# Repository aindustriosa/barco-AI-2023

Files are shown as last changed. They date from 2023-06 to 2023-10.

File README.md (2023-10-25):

# Barco Solar AI-023 A Industriosa
Barco Solar AI-023 A Industriosa

Hemos creado un barco impreso en 3d para participar en la <a href="http://regatasolar.org" target="_blank">Regata Solar de Marine Instruments</a>. Esta vez un trimaran de unos 4Kg de peso y un volumen total de 12 litros.

Se ha diseñado integramente en Cinema 4D, con subdivisión de superficies (curvas Nurbs).

Una vez modelado, se han dividio en 32 piezas para imprimir, secciones de hasta 250x250x200mm y exportado a STL. Para optimizar la impresión intentamos que cada sección no tardase más de 10 horas en imprimirse, para intentar imprimir por el dia y dormir por la noche :P El software de slicer usado es el Simplify3D y la impresora una Ender 5 Plus.

Evitanto el uso de soportes a la hora de imprimir se han hecho algunas secciones que finalmente se pegan para poder imprimir sobre el lado más plano y evitar luego el postprocesado.

Una vez impresas las piezas, y para facilitar la rigidez a la hora de pegarlas, se han hecho unas secciones en cada pieza para pegar y encajar unos pequeños tubos impresos de unos 10x10x50mm. Se ha pegado todas las partes con pegamento para modelismo comprado en bazar chino, tarda unas 4 horas en secar y quedan las piezas muy rígidas. En las zonas que por sharping de las piezas hizo falta se relleno de masilla para carrocerías de Ceys. 

Para darle el acabado final, una vez pegadas todas las piezas, se ha aplicado imprimación de color blanco y posteriormente una mano de Epoxi. En el montaje, en las zonas más irregulares se le aplicó un poco de lijado.

Para encajar las partes de electrónica al barco, así como el soporte de la placa solar, se han usado unos insertos de M5 y M3 aplicados con solador, que evitan el uso de tuercas y hacen que las zonas de enrosque queden bien sujetas.

Para las tapas se ha usado goma Eva cortado en laser para hacer las zonas de unión impermeables.

## Electrónica

Hemos intentado hacer una nueva PCB partiendo de un Attiny1614. Se ha diseñado la pcb en KiCAD, integrando un sensor INA219 para la optimización del voltaje y potencia de la placa solar basandonos en la propuesta de <a href="https://github.com/aindustriosa/Solar_MPPT_board" target="_blank">A Industriosa</a> del año 2019.

Con los limites de potencia y memoria del Attiny1614, hemos implementado el uso del sensor así como un divisor de voltaje para leerlo via VREF. Los mensajes enviados desd eel mando RC al receptor, son procesados por el microcontrolador y en caso de exigirle una velocidad mayor al 30% entra en modo automático, y prioriza el rendimiento que este generando la placa solar en ese momento a optener la velocidad optima sin permitir la caida de potencia por un exceso del rendimiento de la placa solar.

## Materiales

8x PETG 1Kg Blanco 1.75mm (<a href="https://www.amazon.es/dp/B08C4YP5RS/ref=twister_B08HSFRV2M?_encoding=UTF8&th=1" target="_blank">Amazon</a>)

1x Smartfil FLEX - Filamento Flexible (<a href="https://www.smartmaterials3d.com/flex-filamento#/1-tamano-s_330g/26-diametro-175_mm/29-color-sapphire" target="_blank">Smart Materials 3D</a>)
  
3x Tubos cuadrados de 10x10x500mm - <a href="https://www.clipcarbono.com/es/home/947-tubo-exterior-cuadrado-10x10-mm-interior-cuadrado-8x8-mm-de-fibra-de-carbono-longitud-1000-mm.html" target="_blank">Tubo cuadrado, exterior (10x10 mm.) - interior (8x8 mm.) de fibra de carbono - Longitud 1000 mm.</a> Cortesía de <a href="https://www.clipcarbono.com" target="_blank">ClipCarbono</a>

1x Castropox 4307/1209 Resina Epoxi de usos generales (<a href="https://www.castrocompositesshop.com/es/resinas/1099-resina-epoxi-castropox-43071209.html" target="_blank">Castro Composites</a>)

1x Masilla Carrocerias Ceys (<a href="https://www.amazon.es/Desconocido-M59016-Adhesivo-masilla-carrocerias/dp/B00ITVXML6" target="_blank">Amazon</a>)

3x Imprimación Plástico (<a href="https://www.amazon.es/MTN-IMPRIMACIÓN-PLÁSTICOS-400-ML/dp/B00WG2K6W2/ref=sr_1_15?__mk_es_ES=ÅMÅŽÕÑ&crid=2E2QZXNCDXAI6&keywords=imprimacion&qid=1655512005&sprefix=imprimacion%2Caps%2C124&sr=8-15" target="_blank">Amazon</a>)

1x soporte helice y timón (<a href="https://es.aliexpress.com/item/32901476708.html" target="_blank">Aliexpress</a>)

100x Inserto roscado M3 (<a href="https://www.amazon.es/gp/product/B08BCRZZS3/ref=ppx_yo_dt_b_asin_title_o00_s00?ie=UTF8&th=1" target="_blank">Amazon</a>)

6x Inserto roscado M5 (<a href="https://www.amazon.es/gp/product/B07YSVXWS8/ref=ppx_yo_dt_b_asin_title_o00_s00?ie=UTF8&th=1" target="_blank">Amazon</a>)

1x Acoplamiento Motor 4x5mm (<a href="https://www.amazon.es/gp/product/B09LV3KD4H/ref=ppx_yo_dt_b_asin_title_o05_s00?ie=UTF8&th=1" target="_blank">Amazon</a>)

1x Motor NTM Prop Drive 28-30 800KV (<a href="https://hobbyking.com/es_es/propdrive-v2-2830-800kv-brushless-outrunner-motor.html" target="_blank">Hobbyking</a>)

1x Turnigy Multistart 20A V2 ESC (<a href="https://hobbyking.com/es_es/turnigy-multistar-20a-v2-esc-with-blheli-and-4a-lbec-2-6s.html" target="_blank">Hobbyking</a>)

## Enlaces

- <a href="http://regatasolar.org" target="_blank">Regata Solar de Marine Instruments</a>
- <a href="https://www.clipcarbono.com" target="_blank">ClipCarbono</a>
- <a href="http://aindustriosa.org" target="_blank">A Industriosa</a>

Proxecto patrocinado por Xunta de Galicia e Amtega Axencia para a Modernización Tecnolóxica

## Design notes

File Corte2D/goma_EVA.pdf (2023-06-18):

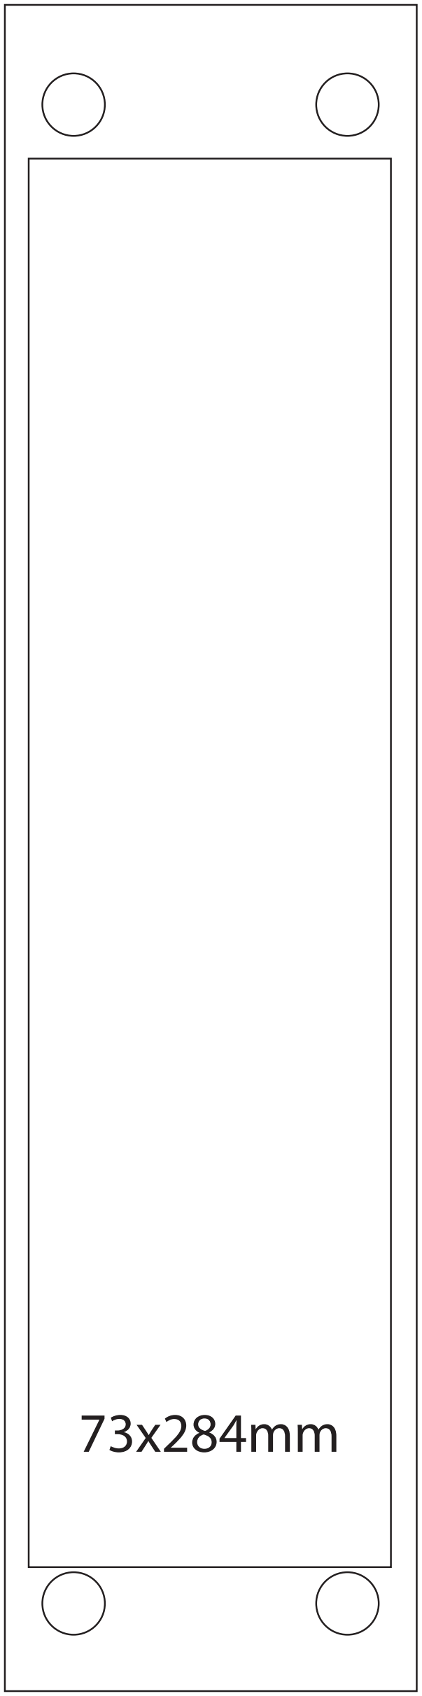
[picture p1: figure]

83x340mm

8x72mm

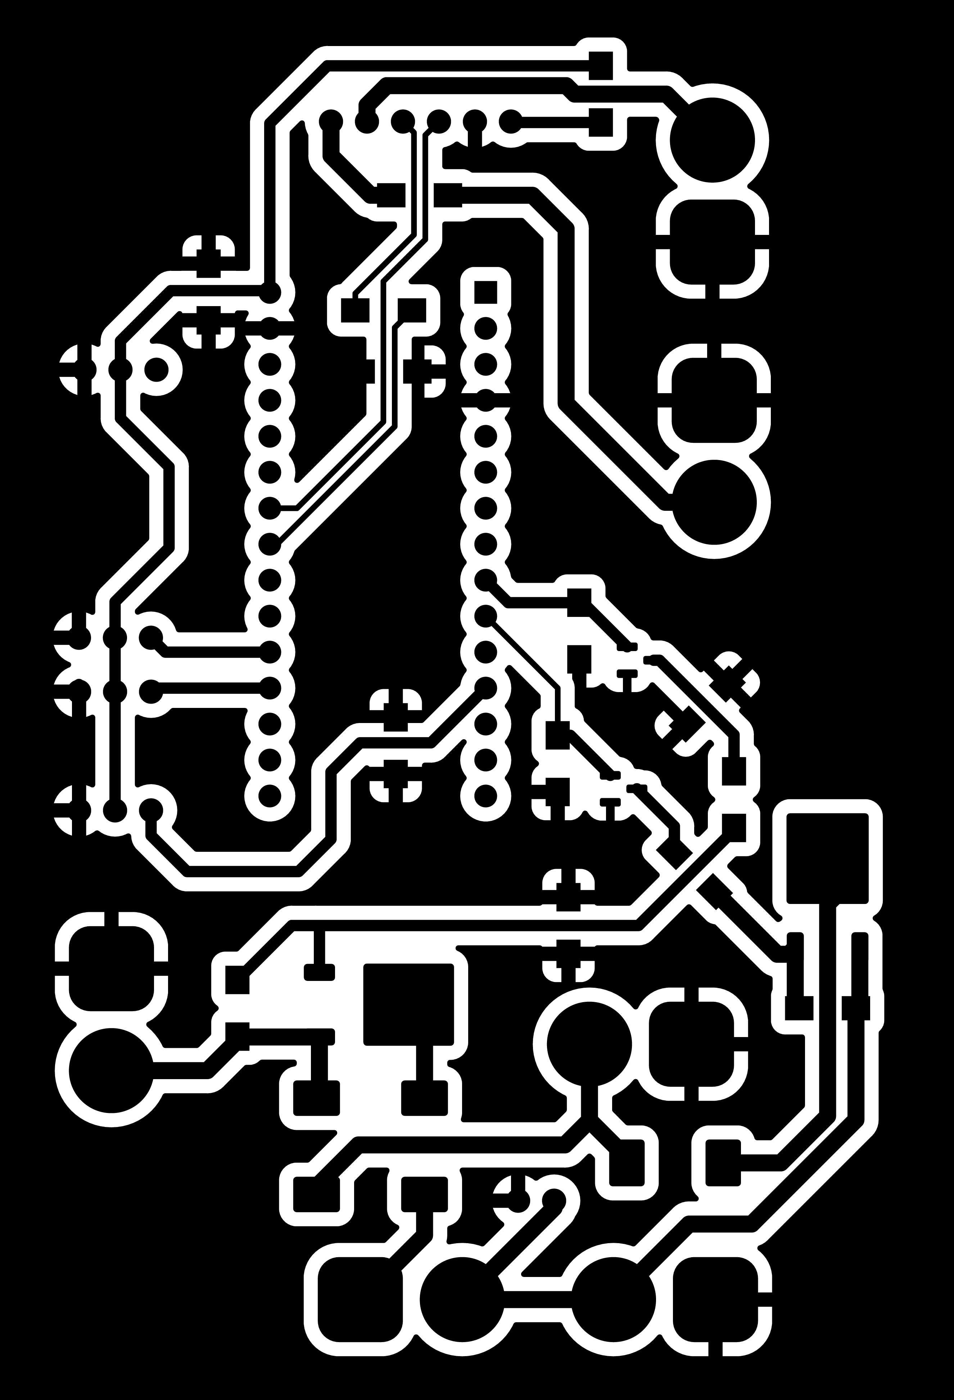
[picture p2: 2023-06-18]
Electrónica/CNC/PCB_Condensadores_PISTAS.png

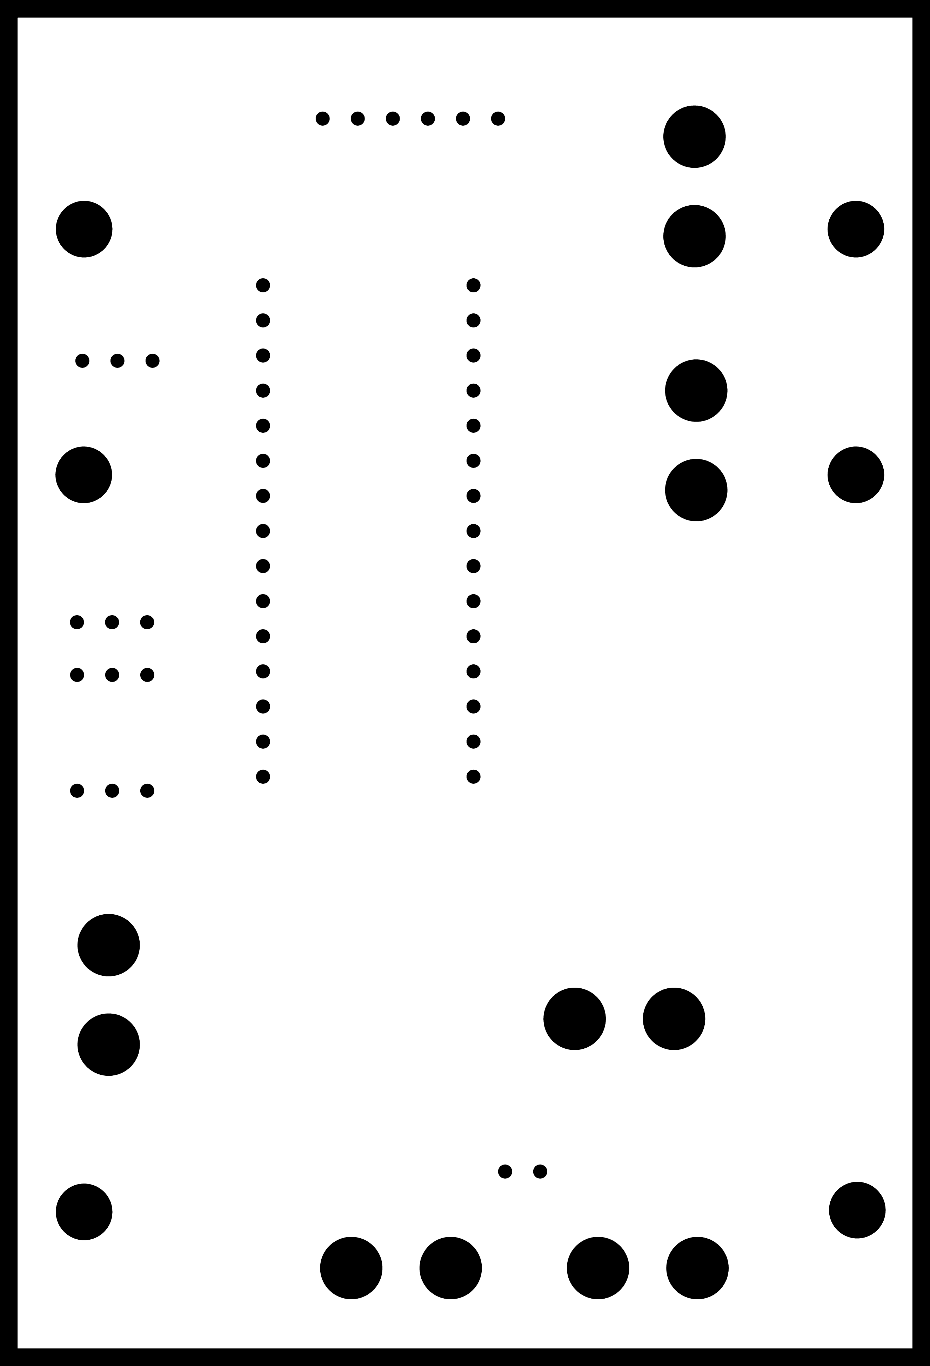
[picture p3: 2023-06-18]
Electrónica/CNC/PCB_Condensadores_CORTE.png

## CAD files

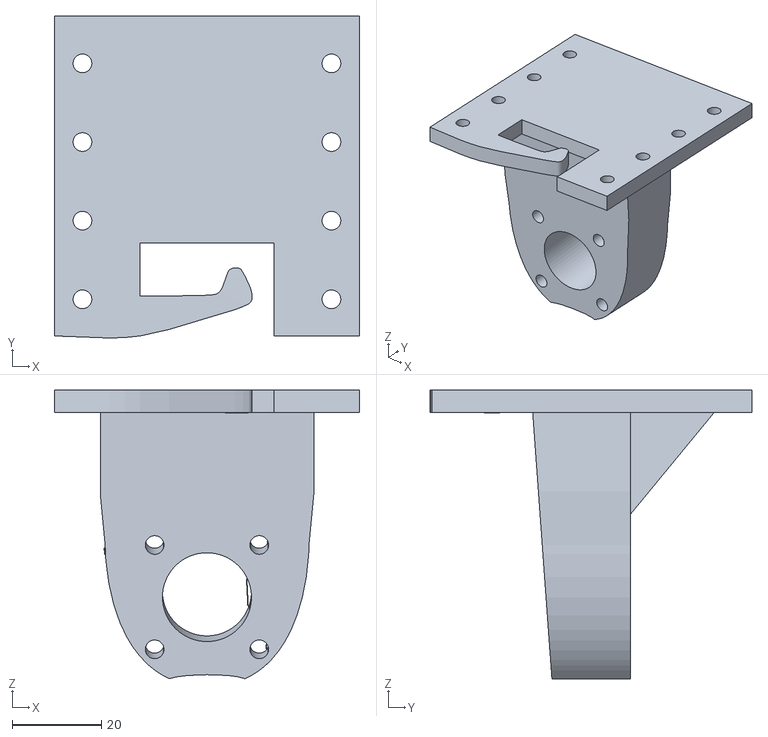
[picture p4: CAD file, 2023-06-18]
STL/Casco/soporte_motor.stl
68.5 x 72.3 x 64.9

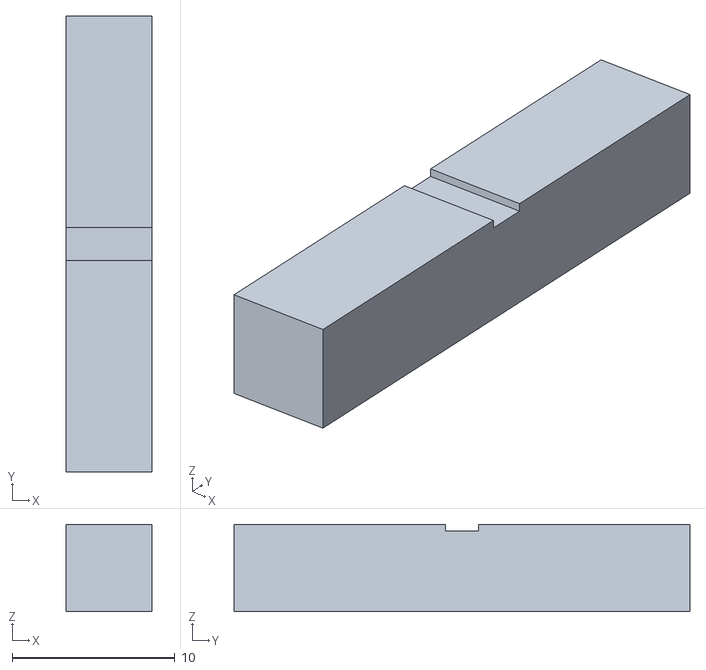
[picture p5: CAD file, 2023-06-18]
STL/Intersecciones/interseccion_6x6x28mm.stl
5.30 x 28.0 x 5.35

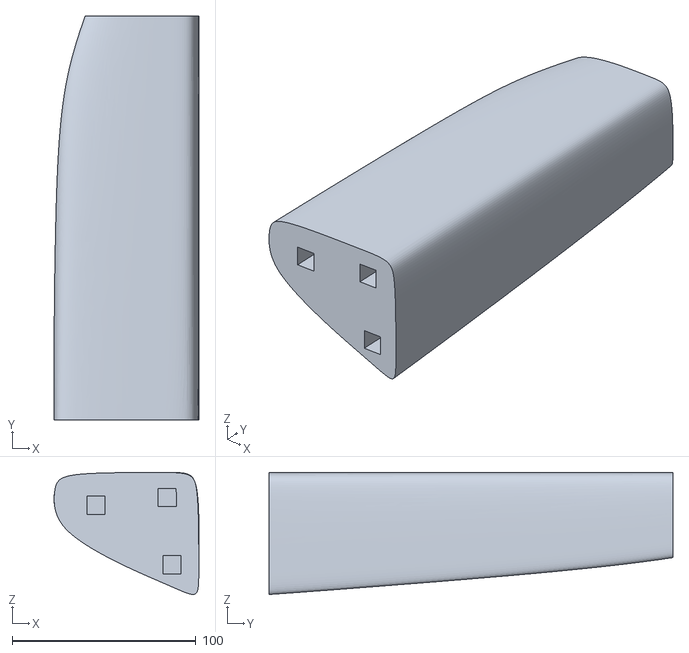
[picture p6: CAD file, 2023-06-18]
STL/Patin/patin_2.stl
79.0 x 220.0 x 66.5

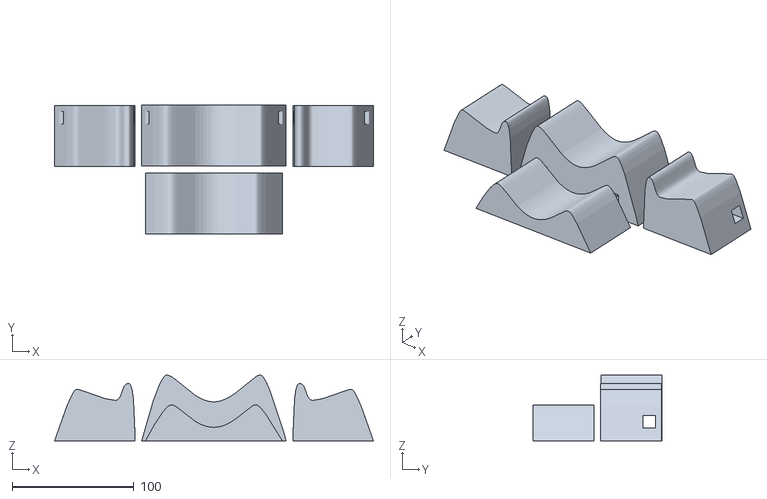
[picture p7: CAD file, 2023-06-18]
STL/soporte-barcoAI-023b_piezas.stl
261.9 x 105.7 x 54.1

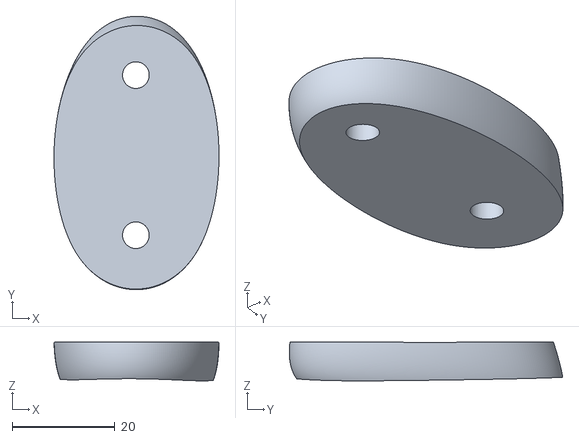
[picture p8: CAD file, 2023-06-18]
STL/Soportes carbono/soporte_detras_TPU.stl
32.2 x 53.3 x 7.55

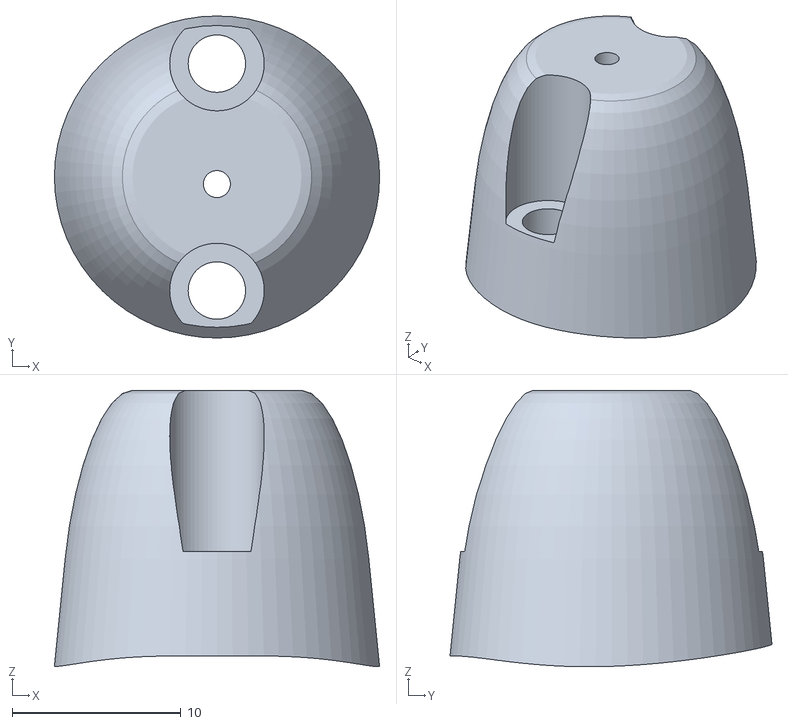
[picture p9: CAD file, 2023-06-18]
STL/Casco/soporte_bandera_TPU.stl
19.3 x 19.1 x 16.4

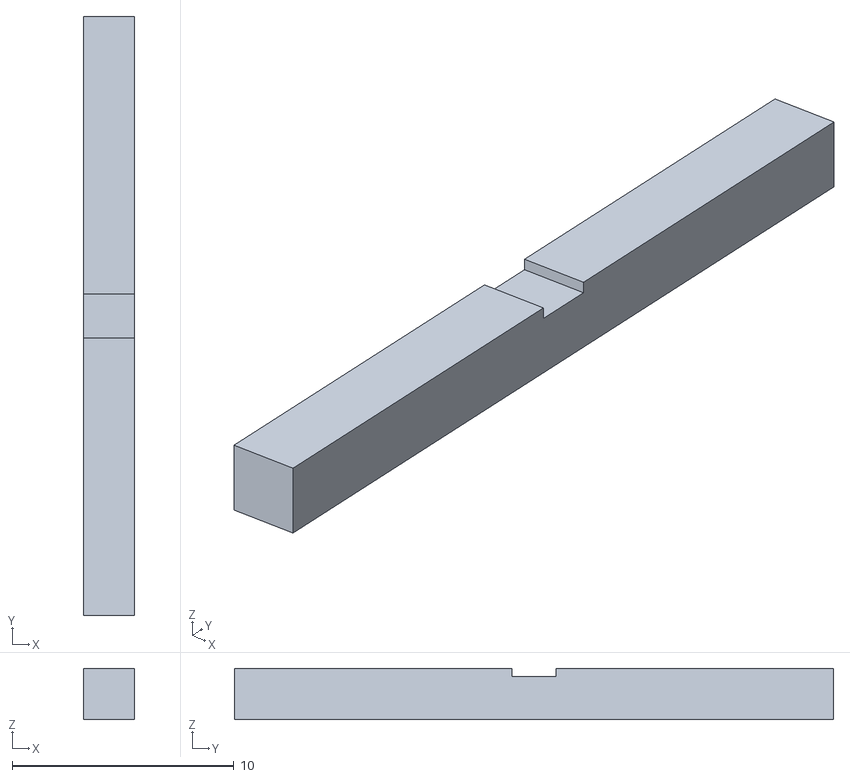
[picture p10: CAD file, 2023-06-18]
STL/Intersecciones/interseccion_3mm.stl
2.30 x 27.0 x 2.30

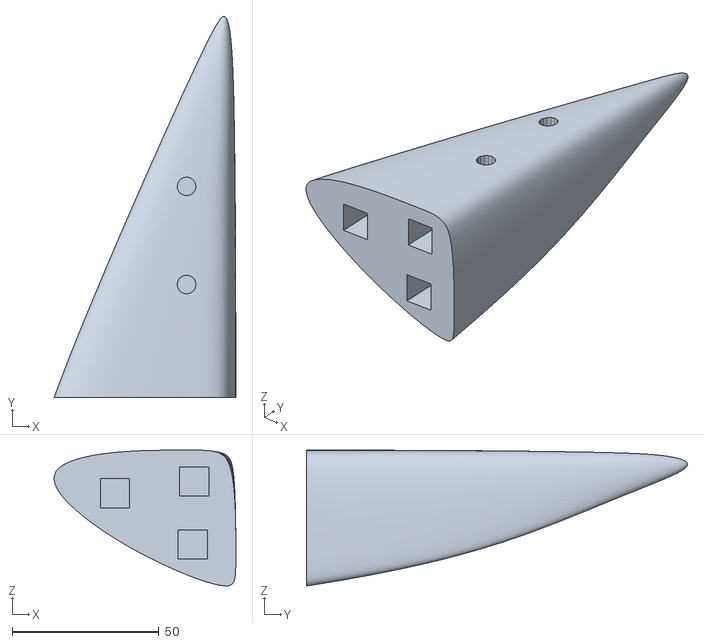
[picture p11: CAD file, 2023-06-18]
STL/Patin/patin_1.stl
62.0 x 130.0 x 46.3

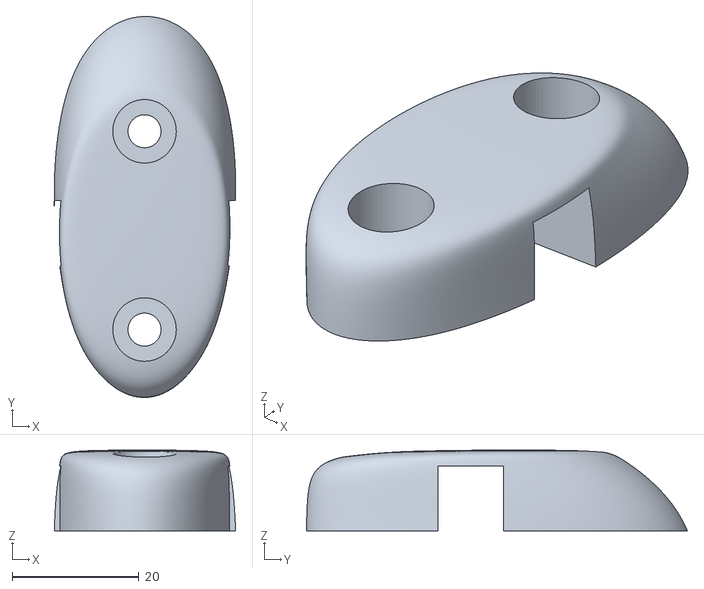
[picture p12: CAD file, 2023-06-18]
STL/Soportes carbono/soporte_medio.stl
28.6 x 60.0 x 12.8

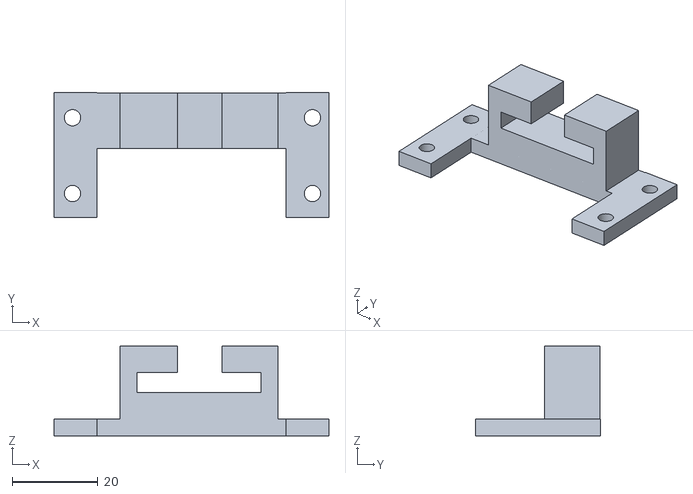
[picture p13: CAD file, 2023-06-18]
STL/Casco/soporte_INA219.stl
64.1 x 29.2 x 21.0

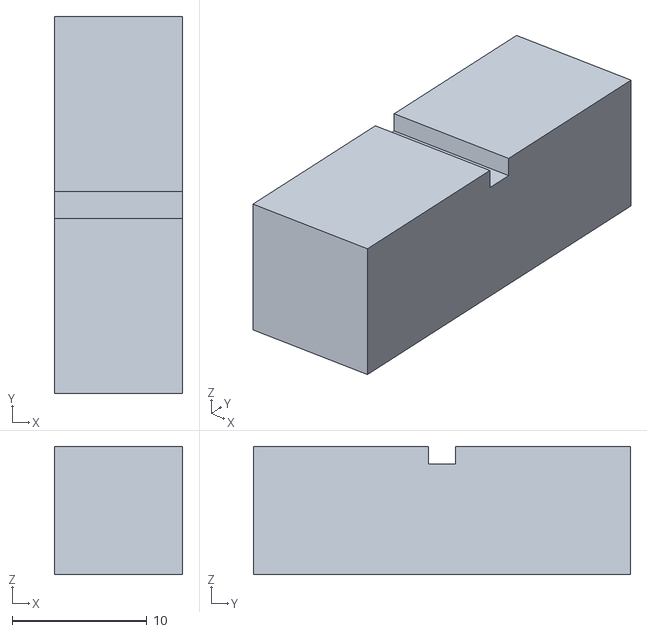
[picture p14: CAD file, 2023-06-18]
STL/Intersecciones/interseccion_10x10x28mm.stl
9.50 x 28.0 x 9.50

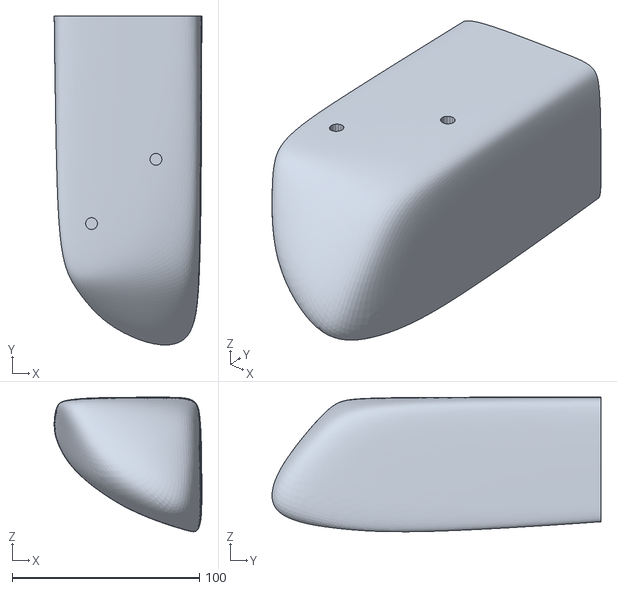
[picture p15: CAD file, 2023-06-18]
STL/Patin/patin_3.stl
78.8 x 175.6 x 71.8

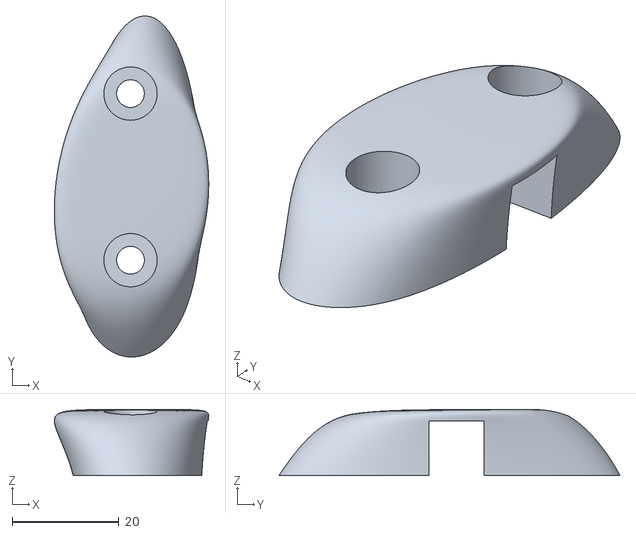
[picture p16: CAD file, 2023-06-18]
STL/Soportes carbono/soporte_patin_delante.stl
29.0 x 63.9 x 12.5

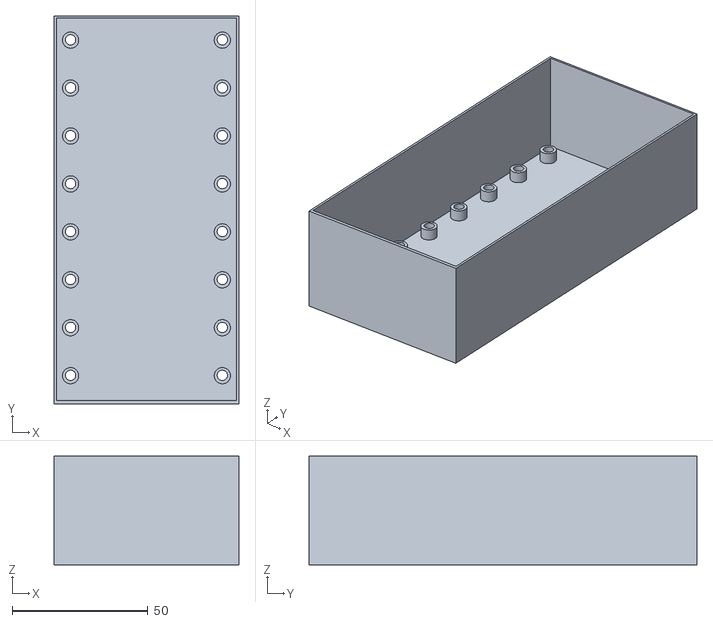
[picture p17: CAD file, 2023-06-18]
STL/Casco/Caja_Electronica.stl
68.0 x 143.0 x 40.0

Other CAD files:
STL/Soportes carbono/soporte_delante_TPU.stl
STL/Casco/soporte_motor_v2.stl
STL/Soportes carbono/soporte_medio_TPU.stl
STL/Casco/caja_bodega.stl
STL/Casco/alimentacion_TPU.stl
STL/Casco/soporte_servo.stl
STL/Casco/tapa_barco.stl
STL/Casco/tapa_barco_antiagua.stl
STL/Casco/tapa_barco_arriba.stl
STL/Soportes carbono/soporte_delante.stl
STL/Soportes carbono/soporte_patin_delante_TPU.stl
STL/Soportes carbono/soporte_patin_detras_TPU.stl

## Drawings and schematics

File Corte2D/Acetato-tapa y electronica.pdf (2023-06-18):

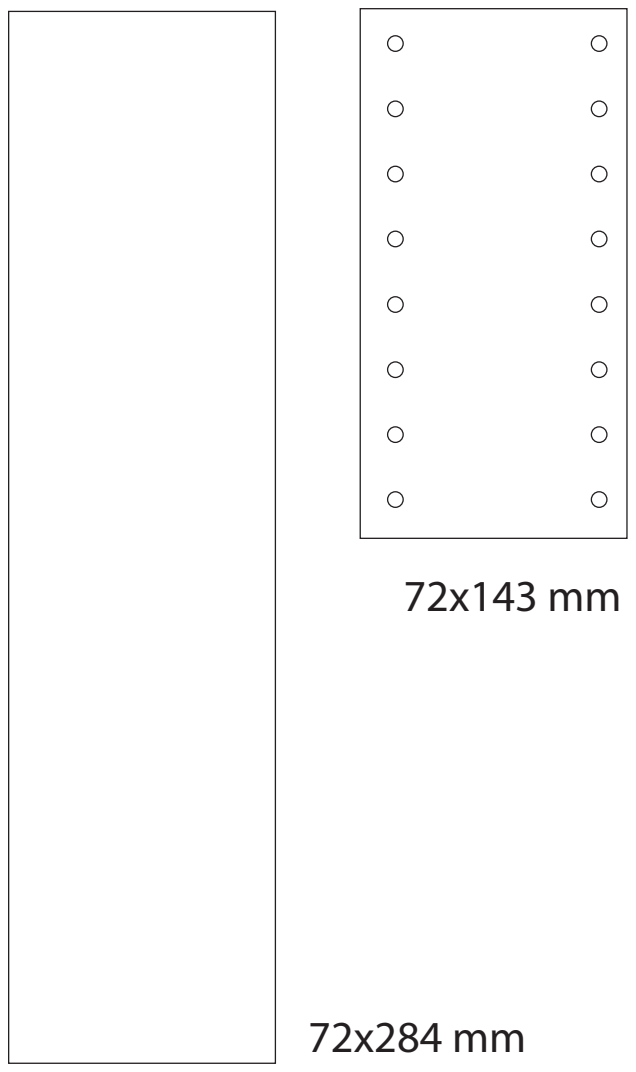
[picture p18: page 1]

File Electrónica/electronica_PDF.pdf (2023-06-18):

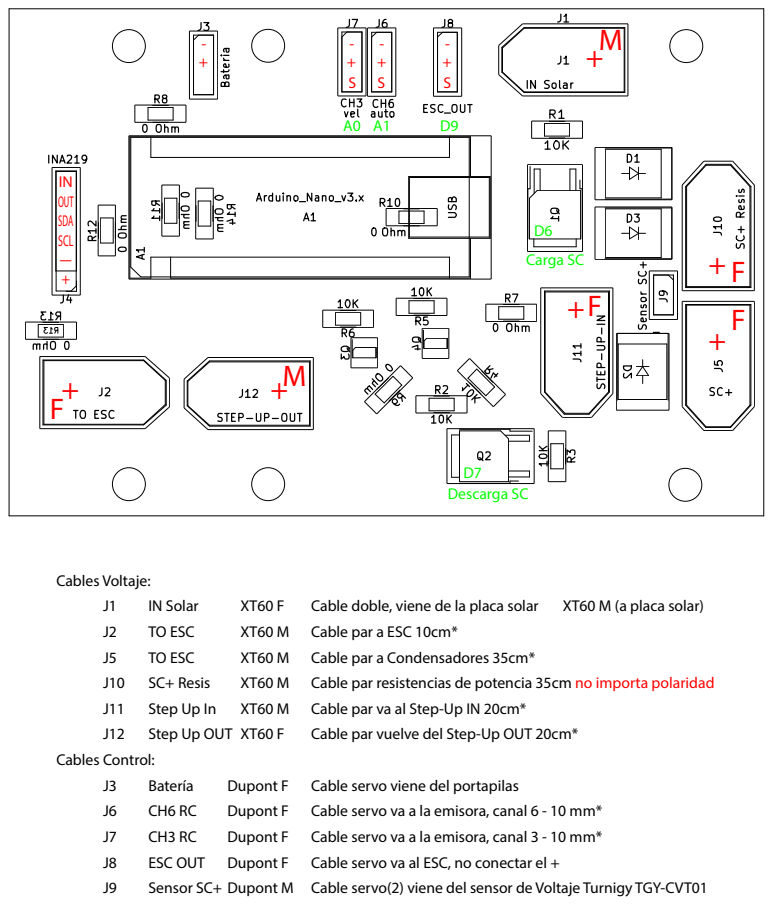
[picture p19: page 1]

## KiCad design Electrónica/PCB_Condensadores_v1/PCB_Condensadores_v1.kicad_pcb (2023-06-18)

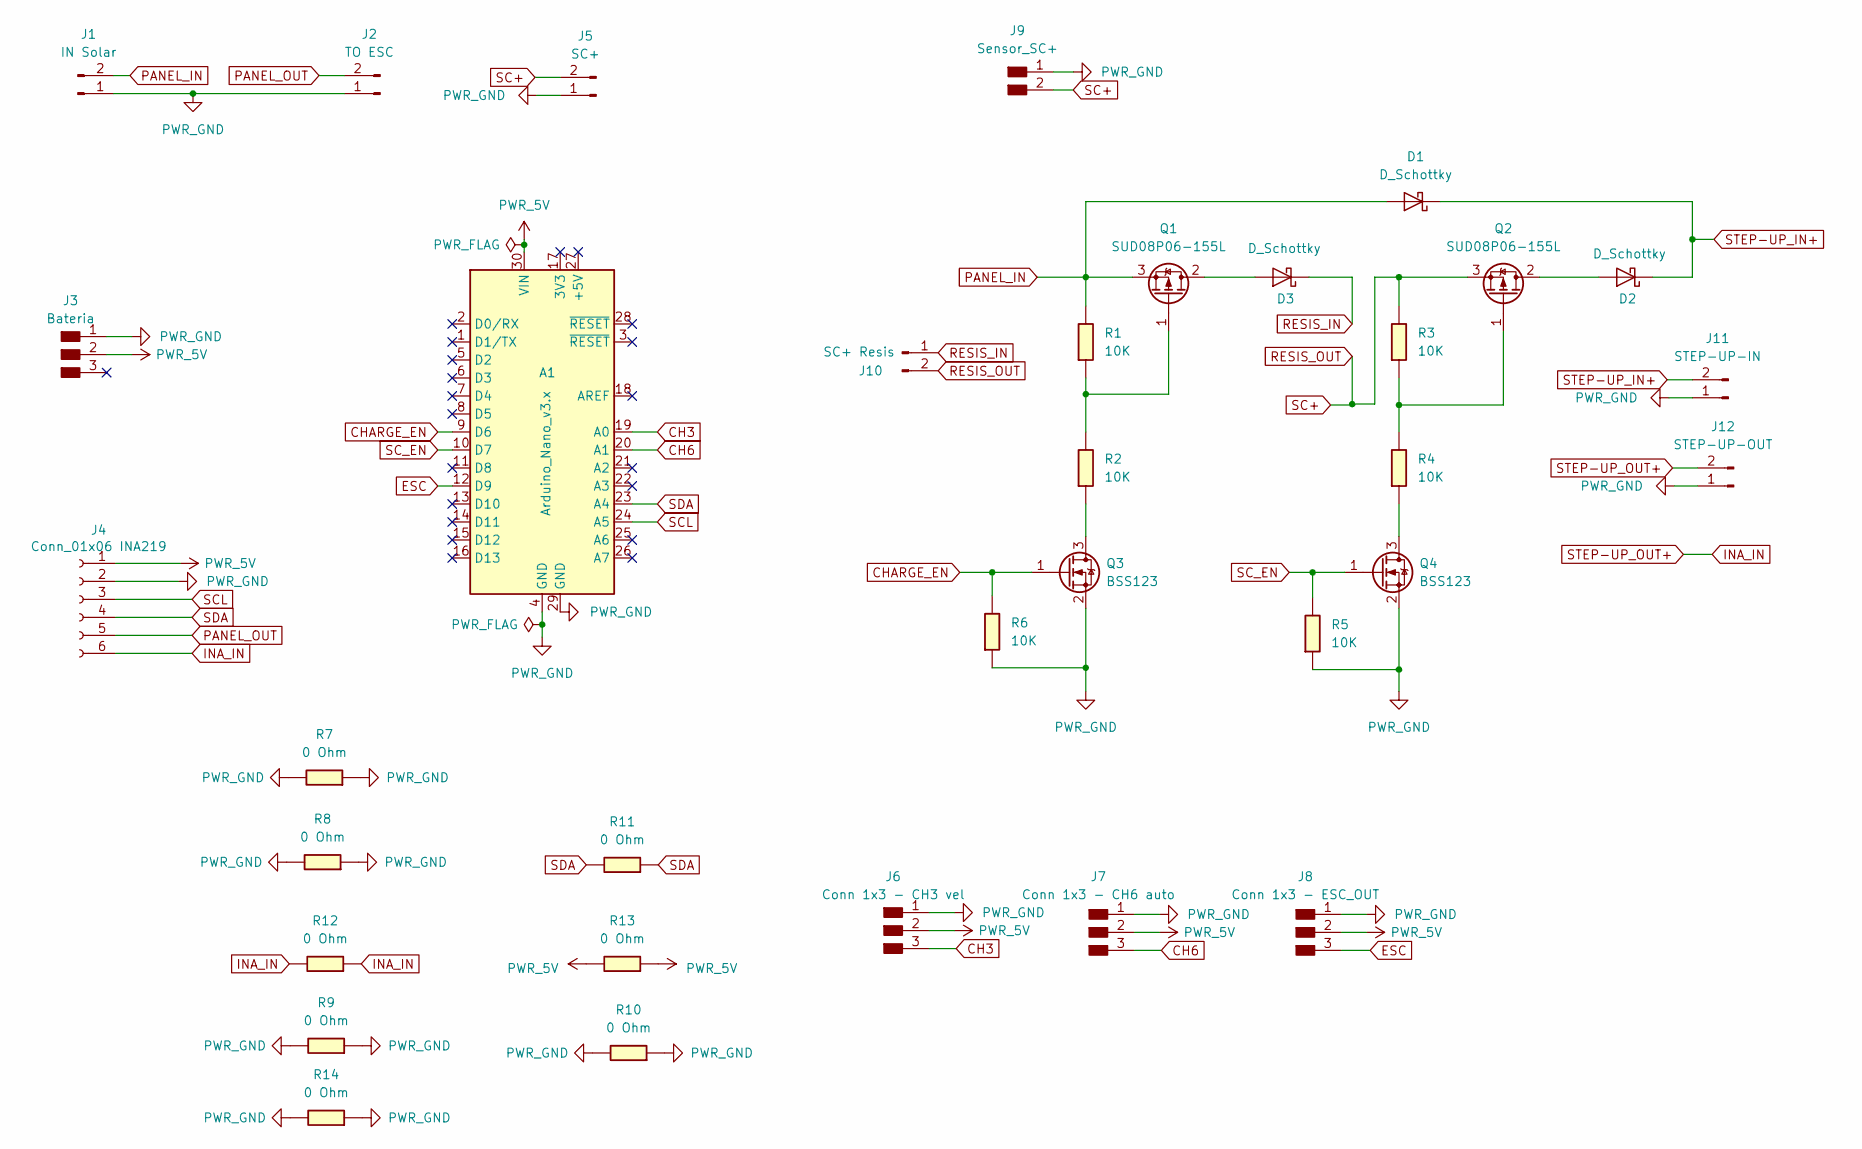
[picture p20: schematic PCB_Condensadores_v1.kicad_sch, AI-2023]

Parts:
A1: Arduino_Nano_v3.x; Arduino_Nano
D1, D2, D3: D_Schottky; D_SMC
J1: IN Solar; AMASS_XT60-F_1x02_P7.20mm_Vertical
J2: TO ESC; AMASS_XT60-M_1x02_P7.20mm_Vertical
J3: Bateria; PinHeader_1x03_P2.54mm_Vertical_THT_D1mm
J4: Conn_01x06 INA219; PinHeader_1x06_P2.54mm_Vertical_THT_D1mm; DIGIKEY_PN SAM1213-06-ND
J5: SC+; AMASS_XT60-M_1x02_P7.20mm_Vertical
J6: Conn 1x3 - CH3 vel; PinHeader_1x03_P2.54mm_Vertical_THT_D1mm
J7: Conn 1x3 - CH6 auto; PinHeader_1x03_P2.54mm_Vertical_THT_D1mm
J8: Conn 1x3 - ESC_OUT; PinHeader_1x03_P2.54mm_Vertical_THT_D1mm
J9: Sensor_SC+; PinHeader_1x02_P2.54mm_Vertical_THT_D1mm
J10: SC+ Resis; AMASS_XT60-M_1x02_P7.20mm_Vertical
J11: STEP-UP-IN; AMASS_XT60-M_1x02_P7.20mm_Vertical
J12: STEP-UP-OUT; AMASS_XT60-F_1x02_P7.20mm_Vertical
Q1, Q2: SUD08P06-155L; TO-252-2
Q3, Q4: BSS123; SOT-23
R1, R2, R3, R4, R5, R6: 10K; R_1206
R7, R8, R9, R10, R11, R12, R13, R14: 0 Ohm; R_1206

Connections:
CH3: A1.19 (A0), J6.3
CH6: A1.20 (A1), J7.3
CHARGE_EN: A1.9 (D6), Q3.1 (G), R6.1
ESC: A1.12 (D9), J8.3
INA_IN: J4.6, J12.2, R12.1, R12.2
unnamed: D2.2 (A), Q2.2 (D)
unnamed: D3.2 (A), Q1.2 (D)
unnamed: Q1.1 (G), R1.2, R2.1
unnamed: Q2.1 (G), R3.2, R4.1
unnamed: Q3.3 (D), R2.2
unnamed: Q4.3 (D), R4.2
PANEL_IN: D1.2 (A), J1.2, Q1.3 (S), R1.1
PANEL_OUT: J2.2, J4.5
PWR_5V: A1.30 (VIN), J3.2, J4.1, J6.2, J7.2, J8.2, R13.1, R13.2
PWR_GND: A1.4 (GND), A1.29 (GND), J1.1, J2.1, J3.1, J4.2, J5.1, J6.1, J7.1, J8.1, J9.1, J11.1, J12.1, Q3.2 (S), Q4.2 (S), R5.2, R6.2, R7.1, R7.2, R8.1, R8.2, R9.1, R9.2, R10.1, R10.2, R14.1, R14.2
RESIS_IN: D3.1 (K), J10.1
RESIS_OUT: J5.2, J9.2, J10.2, Q2.3 (S), R3.1
SCL: A1.24 (A5), J4.3
SC_EN: A1.10 (D7), Q4.1 (G), R5.1
SDA: A1.23 (A4), J4.4, R11.1, R11.2
STEP-UP_IN+: D1.1 (K), D2.1 (K), J11.2

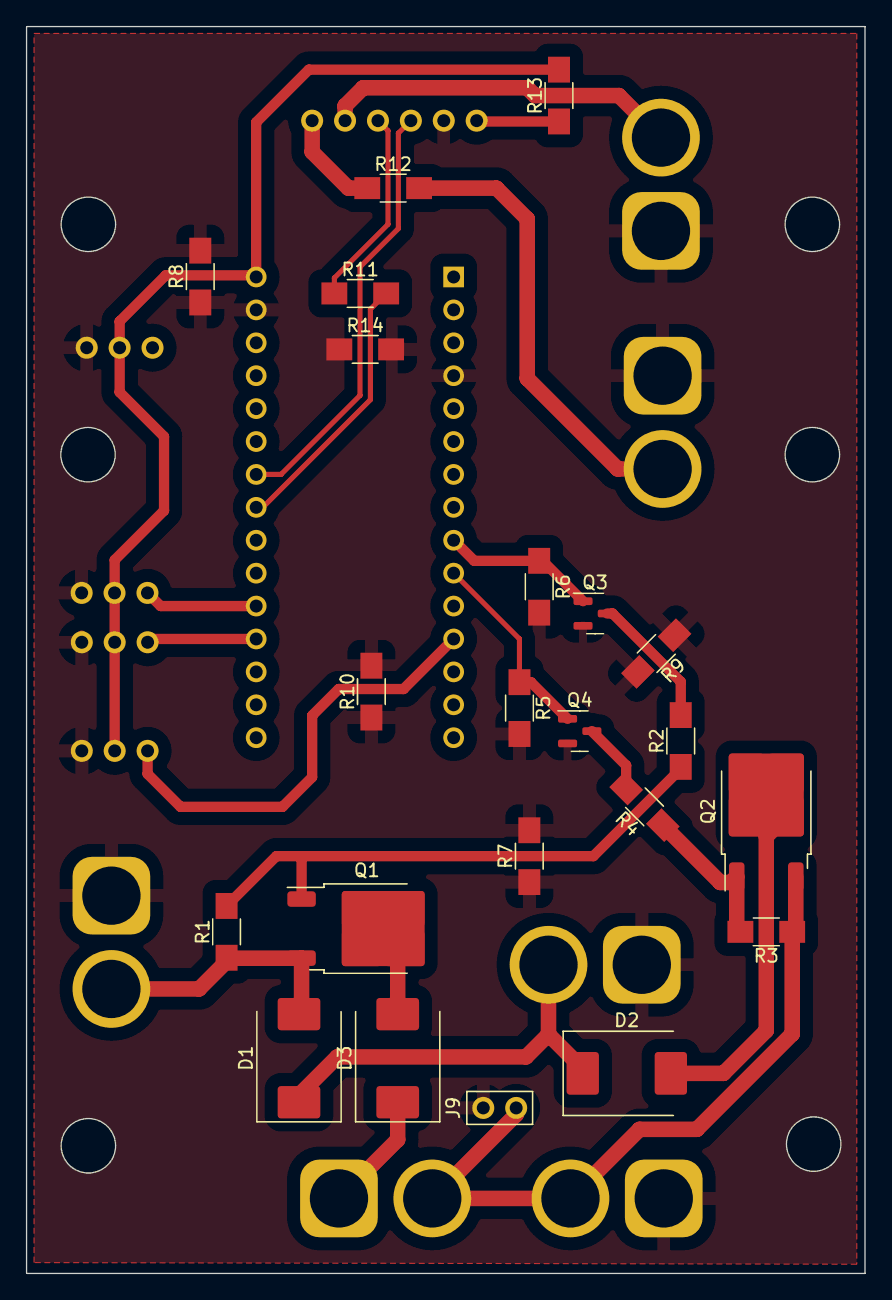
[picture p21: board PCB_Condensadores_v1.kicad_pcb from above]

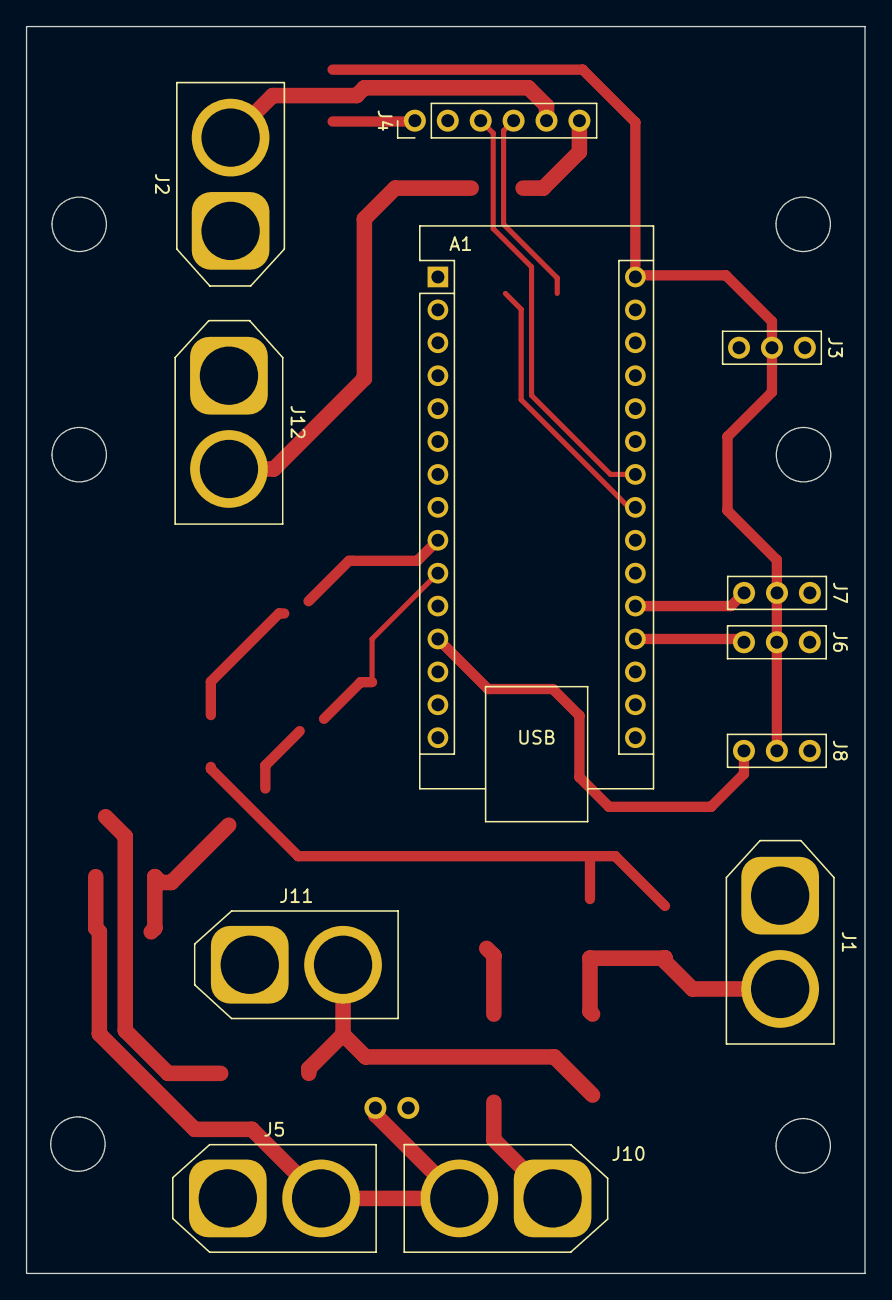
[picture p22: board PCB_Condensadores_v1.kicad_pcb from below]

Board: 2 copper layers, 64.7 x 96.2 mm, 34 parts (12 on the bottom side), 21 nets.

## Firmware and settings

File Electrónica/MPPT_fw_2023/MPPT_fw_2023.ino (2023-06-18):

#include <Streaming.h>  //para la salida de print y endl http://arduiniana.org/libraries/streaming/
#include <EEPROM.h>
#include "esc.h"
#include "Ticker.h"
#include "current.h"
#include "Config.h"


//---------------DEBUG---------------
//#define PIN_DEBUG 8
bool DEBUG = true;
//-------------------P&O SETTINGS--------------
Ticker PO_timer;

#define PO_ENABLE_SPEED 100 // 30 se activa el INA
#define PO_TIMER 150
#define PO_STEP 1
#define po_samples 10
float v = 0;
float i = 0;
float p = 0;
float Av = 0;  //Delta Volts
float Ap = 0;  //Delta Power
float p_prev = 0;
float v_prev = 0;

float i_media = 0;
float v_media = 0;
int cnt_po = 1;
int cnt_po_ina_samples = 0;
int po_speed = 0;  //valor d po_speed cuando entramos en po
bool po_enable = false;
void PO_timer_callback();

//-------------------RC SIGNAL-----------------
static byte rcOld;
volatile unsigned long rcRises[4];
volatile unsigned long rcTimes[4];
volatile unsigned int rcChange = 0;
void init_RC();

//-----------------ESC----------------------
#define sensibilidad 3
int speed = 0;

int control_SC = 0;
String estado;

//-----------------INA219---------------
#define Ki 270
#define Kv

//--------------Supercondensador--------------

#define Charge_SC 6
#define SC_EN 7



ISR(PCINT1_vect) {
  byte rcNew = PINC & 15;        //PINC & 1111 pilla el estado de los pines A0-A3
  byte changes = rcNew ^ rcOld;  //saca el pin que ha cambiado comparando el estado de los 4 anteriores cn s 4 nuevos
  byte channel = 0;
  unsigned long now = micros();
  while (changes) {                                 // de 0000 a 1111
    if ((changes & 1)) {                            //Ha cambiado este canal ?
      if ((rcNew & (1 << channel))) {               //si es flanco subida
        rcRises[channel] = now;                     //t0=ini
      } else {                                      //si es flanco bajada
        rcTimes[channel] = now - rcRises[channel];  //t1=nw-t0;
      }
    }
    changes >>= 1;
    ++channel;
    ++rcChange;  //activamos la flag de nuevos cambios para el loop
  }
  rcOld = rcNew;
}


void setup() {
  Serial.begin(9600);

  //pinMode(PIN_DEBUG,INPUT);

  init_ESC();
  delay(1000);
  init_RC();

  init_INA219(0);

  PO_timer.setCallback(PO_timer_callback);
  PO_timer.setInterval(PO_TIMER / po_samples);
  PO_timer.start();

  po_enable = false;  //indicamos que iniciamos en speed
  Serial.println("TX_PPM,Mode,ESC_PPM,Voltage,Current,Power");
  Serial.println();

pinMode(Charge_SC,OUTPUT);
pinMode(SC_EN,OUTPUT);

  digitalWrite(Charge_SC, 0);
  digitalWrite(SC_EN, 0);
}


void loop() {
  unsigned long rcT[4];
  unsigned int rcN;

  if (rcChange) {
    cli();
    rcN = rcChange;
    rcChange = 0;  //borramos la flag de nuevos cambios
    //leemos los registros de tiempos d cada puerto
    rcT[0] = rcTimes[0];
    rcT[1] = rcTimes[1];
    rcT[2] = rcTimes[2];
    rcT[3] = rcTimes[3];
    sei();

    speed = map(rcT[0], 1000, 2000, 0, 100);

    
    
    //speed = speed/sensibilidad;


// Control carga SC

    control_SC = map(rcT[1], 1000, 2000, 0, 100);

  
      if (control_SC < 25) { // menos de 25% de switch Canal 5, abrimos carga de SC y cerramos descarga
        digitalWrite(Charge_SC, 1);
        digitalWrite(SC_EN, 0);
        estado = "Carga";
      }
      if (control_SC > 25 && control_SC < 75) { // más de 25% y menos de 75% de switch Canal 5, cerramos carga de SC y  descarga
        digitalWrite(Charge_SC, 0);
        digitalWrite(SC_EN, 0);
        estado = "Nada";
      }
      if (control_SC > 75) { // más de 75% de switch Canal 5, cerramos carga de SC y abrimos descarga
        digitalWrite(Charge_SC, 0);
        digitalWrite(SC_EN, 1);
        estado = "Descarga";
      }
 

    if (speed > 100) {
      speed = 100;
    }
    //Serial.println(rcT[0]);
  }
  sei();
  PO_timer.update();
}

void print_telemetry() {

   Serial.println("TX_PPM,Mode,ESC_PPM,Voltage,Current,Power");
 
  Serial.print(speed);
  Serial.print(",");
  if (po_enable) {
    Serial.print("10,");  //modo P
    Serial.print(po_speed);
  } else {
    Serial.print("5,");  // modo s
    Serial.print(speed);
  }
  Serial.print(",");
  Serial.print(v);
  Serial.print(",");
  Serial.print(i);
  Serial.print(",");
  Serial.println(p);
Serial.print(control_SC);
Serial.print(",");
Serial.println(estado);
  Serial.println();
  
}

void PO_timer_callback() {

  if (cnt_po_ina_samples < po_samples) {  //samplea cada 150/10 --> 15ms
    v_media += get_LoadVolts();
    i_media += get_LoadCurrent() / Ki;
    cnt_po_ina_samples++;

  } else {  // Al los 10 samples 10*15 --> 150ms se ejecuta el P&O

    v = v_media / po_samples;
    i = i_media / po_samples;
    p = i * v;
    Av = v - v_prev;
    Ap = p - p_prev;

    //DEBUG = digitalRead(PIN_DEBUG);
    if (speed < 0) speed = 0;
    if (speed < PO_ENABLE_SPEED) {  //Si po_speed <50, vel fijada x mando
      po_enable = false;            //indicamos que estamos en modo speed
      vel_ESC(speed);
      cnt_po = 1;  //reseteamos indicador de P&O para que cuando comience se resetee en ciclo 1 y pille speed
    } else {       //Si po_speed >50 entra P&0
      /*
                ----------COMIENZA P&O--------------------
                */

      if (cnt_po != 1) {
        if (Ap == 0) {
          po_speed += PO_STEP;
          //Serial.println("AP=0");
        } else {
          if (Ap > 0) {
            //Serial.println("AP>0");
            if (Av < 0) {
              po_speed += PO_STEP;
              vel_ESC(po_speed);
              //Serial.println("B2");

            } else if (Av >= 0) {
              po_speed -= PO_STEP;
              vel_ESC(po_speed);
              //Serial.println("B1");
            }
          } else {
            //Serial.println("AP<0");
            if (Av > 0) {
              po_speed += PO_STEP;
              vel_ESC(po_speed);
              //Serial.println("A2");
            } else if (Av <= 0) {
              po_speed -= PO_STEP;
              vel_ESC(po_speed);
              //Serial.println("A1");
            }
          }
        }
      } else {  //Es l primer sample de PO
        po_enable = true;
        po_speed = PO_ENABLE_SPEED;
        po_speed += PO_STEP;
      }



      cnt_po++;
      /*
                ----------FIN P&O--------------------
                */

    }  //end if vel o P&or

    p_prev = p;
    v_prev = v;

    v_media = 0;
    i_media = 0;
    cnt_po_ina_samples = 0;  //reseteamos contador de samples para k comience con los sig 10

    if (DEBUG) {
      print_telemetry();
    }

  }  //end loop samples

}  //end fnct

void init_RC() {
  rcOld = 0;
  pinMode(A0, INPUT);
  pinMode(A1, INPUT);
  pinMode(A2, INPUT);
  pinMode(A3, INPUT);
  PCMSK1 |= 0x0F;  //pin-change interrupt en los 4 primeros pines del PORTC (A0-A3)
  PCIFR |= 0x02;   //clear pin-change interrupt
  PCICR |= 0x02;   //pin-change interrupt enable
}
